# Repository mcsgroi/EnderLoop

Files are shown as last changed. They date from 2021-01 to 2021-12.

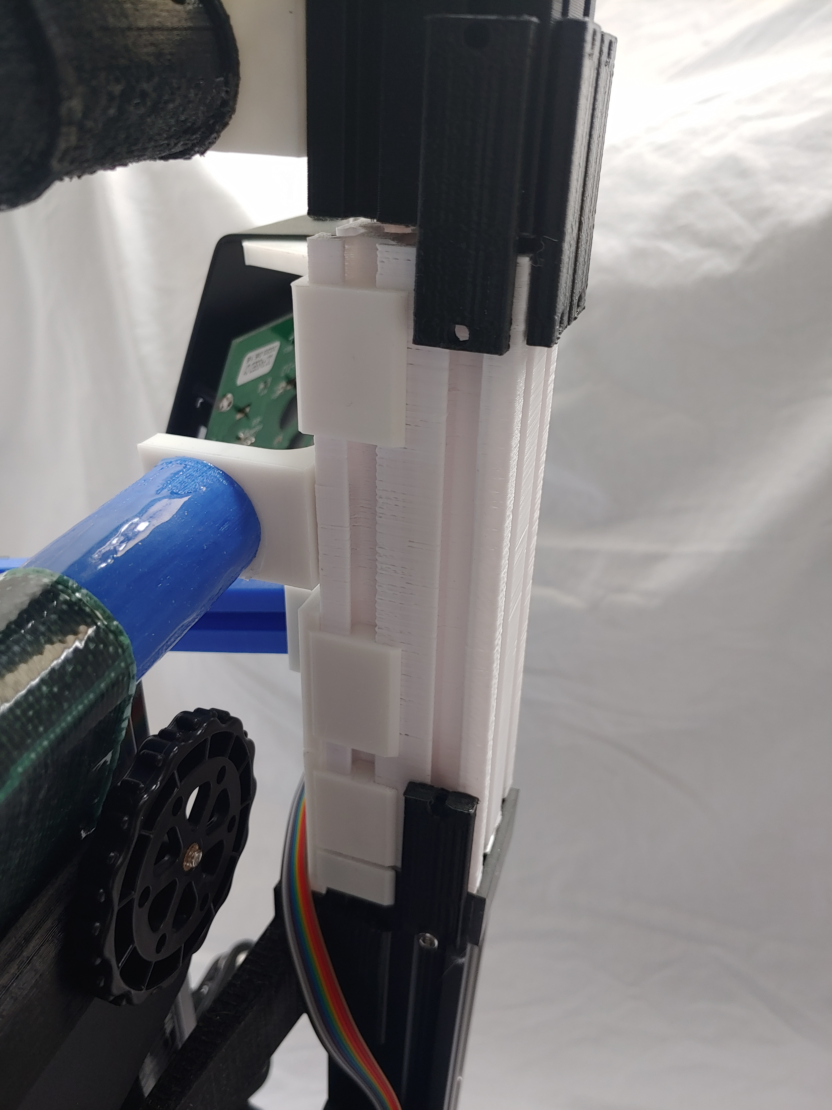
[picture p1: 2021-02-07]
Images/Printer/bottom3.jpg

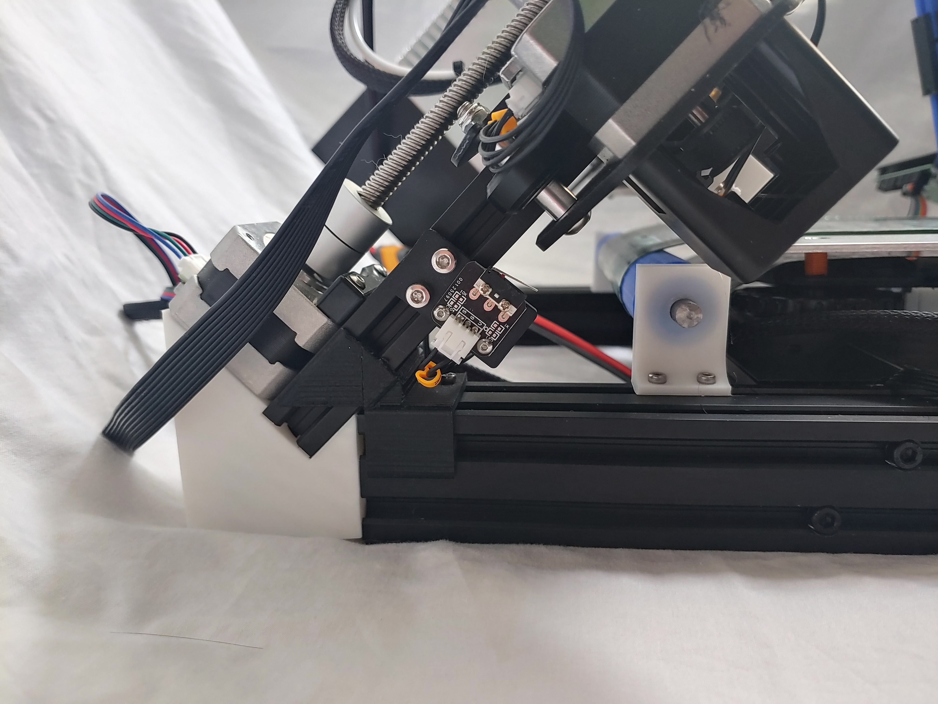
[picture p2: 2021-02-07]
Images/Printer/left5.jpg

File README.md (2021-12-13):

# EnderLoop
This supports around a 110x200xinfinity bed size.

[Here](https://www.youtube.com/watch?v=L337KpcwrPk&feature=youtu.be)'s a great video with Adam at PowerBelt3D discussing the EnderLoop.

### Donations
If you find this project helpful and want to send me a cup of coffee, feel free to use this button



&nbsp; 
&nbsp;  
&nbsp;  
**What's in this project:**

#### Pictures
I've attached a few pictures. Models in the printer pictures should mirror what is in the latest source files. Any differences should be minimal and are usually just that I'm running a slightly older version of the model to save on plastic waste. I've also included some test print pics to demonstrate the quality of what I'm getting off of the EnderLoop. In the pictures with two benchies, the black one is off of the belt printer whereas the white one is from a CR-6 SE as a comparison point.

#### Models
Not all of these models are required. I have included a list of what you'll need to print out and how many of each.

#### Firmware
The firmware will need to be flashed to the printer before you attempt to use it. I've included information on this in the instructions, but I've included my latest build of the firmware as well as the source in case you feel like modifying it. If you notice any issues feel free to open an issue or a PR on Github.

#### BlackBelt Cura Config
This is the configuration for the slicer. I've also included a couple snapshots in the pictures folder of what I'm using for settings on my printer currently, but keep in mind that any number of variables could change those for you (material, printer "quirks", etc.).

#### Test Models
Some test models for verifying the printer (esteps, angle, and long print adhesion). Note that the long print, as you'd probably expect, uses a large amount of material so, if you want to print that, I'd dial in smaller prints first.

### Versions
Check under the releases tab for stable snapshotted versions of this project. You can always use what is in the master branch, but since it is fluctuating with new work, there may be incorrect information or incompatible parts/software (though I try to keep everything in sync).

## Note
This is still a work in progress and you will most definitely find issues. Currently, I've identified a couple outstanding problems in my build:
1. Adhesion. I'm just gonna say outright that this isn't terrible adhesion. It's just not as good as I like it. It really depends on the model height and surface area touching the belt. You can improve the adhesion slightly by "scuffing" the surface of the belt with sandpaper.
2. Slight angle on some parts. I believe this has to do with esteps or cooling.

Most of the remaining issues are fairly minor and should either be small model updates or software tweaks.

If you experience any issues, they are most likely a result of bed leveling. I learned this the hard way so certainly check this first. Bed leveling a belt printer is trickier than with a "normal" printer and can cause some strange issues (adhesion, angled prints, head collisions, etc.)

Lastly, I'll note, and this is less of an issue and more of a limitation, but this will print slower than a normal printer due to the lead screw being used as the "de facto Y axis".

### Parts

#### Printed Parts
* 2 - AngledSupport
* 2 - BedStandV2
* 2 - BeltSlide
* 1 - EndSensorHolder
* 2 - GantryBraceBottom
* 1 - GantryBraceHolderLeft
* 1 - GantryBraceHolderRight
* 2 - GantryBraceTop
* 1 - LcdHolder
* 1 - LeftBeltClip
* 1 - ModifiedMotorHolder
* 1 - PartCoolerVent
* 1 - RightBeltClip
* 2 - Updated45ZHolder
* 2 - UpdatedAxle or UpdatedAxleCrowned or UpdatedAxleSteelRod
* 4 - UpdatedYIdler
* 2 - YExtension
* 2 - YExtensionClamp
* 11 - YExtensionSupport

##### Optional

1 - Scraper

###### Extension rollers
* 2 or 3 - UpdatedAxle
* 4 or 6 - UpdatedYIdler
* 2 - Yextension
* 8 - YExtensionSupport

#### Purchased Parts
##### Belt
Currently there are 3 options (there may be a 4th option when Creality's CR-30 belt is officially released):
1. Buy a custom belt. There are some sites that are willing to sell a custom belt. I believe BuildTak is willing to custom make a belt, however the price is fairly steep (based on my research on the WhiteKnight printer).
2. DIY. I'll include a section here on how to make a belt yourself should you want to. Note that it's going to take some patience to get a clean surface and the performance (adhesion and ability of the roller to grip the belt) will be worse than option 3. The price point for this option is also going to be about the same as option 3.
3. [POWERBELT3D Belt](https://powerbelt3d.com/product/formula32-conveyor-belt-for-enderloop/). I've reached out to Adam at PowerBelt and he was willing to list a custom belt that he has been working on that is specifically designed for the EnderLoop on his store. This is what I use right now and has pretty good characteristics. A couple of notes from the PowerBelt folks on this:
	* For PLA, we recommend a bed temperature of 60-70C.  
    * For PETG and TPU, they recommend a bed temperature of 70-80C. PETG tends to stick  _very_  well to the Polyester top layer, and might rip the material. They also recommend applying glue stick to the conveyor belt as a release agent to prevent this. If tearing still occurs, increasing the speed of outer contour that contacts the conveyor belt may help.

#####  Timing Belt
You have a few options. My recommendation would be to purchase https://www.amazon.com/gp/product/B081GYFQM3/ref=ppx_yo_dt_b_asin_title_o07_s00?ie=UTF8&psc=1
These are a little over 8mm wide. You'll note that this is wider than standard 2GT time belts (typically 6mm).
This helps it get better traction.
If you are looking to save a few bucks, you should also be able to use the extra timing belt in the Ender 3 
kit you don't need (for the original y axis). I would recommend looking up videos on joining timing belts, 
but you should be able to cut each end in the middle of a tooth (keeping note of how long you want the loop), 
rough up the back of the belt (smooth side) with sand paper, and glueing them together with a piece of 
cloth or ribbon on the roughed up side for extra adhesion support. If you find that this isn't enough to hold the belt together, 
you can try to use braided fishing line (https://www.amazon.com/gp/product/B076CMSC63/ref=ppx_yo_dt_b_asin_title_o09_s00?ie=UTF8&psc=1) 
to stitch the adhered ends together.

#####  Belt Motor
The Y motor on the Ender 3 simply doesn't have enough torque to be able to turn the belt.
I ended up purchasing https://www.amazon.com/gp/product/B07PS4BMSN/ref=ppx_yo_dt_b_asin_title_o03_s00?ie=UTF8&psc=1.
It is a Nema 17 stepper motor that draws less than 2 Amps (this is the max that the drivers on the Ender 3, regardless of version, will support).
That stepper motor I linked also coincidentally has an extra cable with it. You will either need this, 
another long stepper cable, or to make your own cable 
(https://www.amazon.com/gp/product/B077LYP4T9/ref=ppx_yo_dt_b_asin_title_o02_s00?ie=UTF8&psc=1). This is to accomodate the longer distance to the 
original Z motor which mounts at the back of the printer now, instead of the middle.
##### Pulley
Since you need to install a new motor, you will also need a new pulley for the belt motor. I used https://www.amazon.com/gp/product/B07BT6N12L/ref=ppx_yo_dt_b_asin_title_o05_s00?ie=UTF8&psc=1
#####  Springs
You will need better springs for the bed than the Ender 3 comes with. I ended up buying this assortment https://www.amazon.com/gp/product/B07V6YCYP5/ref=ppx_yo_dt_b_asin_title_o00_s00?ie=UTF8&psc=1
##### "Grippy" Paint
You will also need flex seal or another suitably "grippy" paint on coating to put on the axle.
##### Lubricant
You will need a lubricant for all of the roller ends. I always use Super Lube.

##### Steel Rods - Optional
I'm listing this here even though it is optional because I **highly** recommend this. These are for the rollers to ensure they don't flex inward. You can make this work without them, but the purely 3d printed one's can't continually handle the stress of sitting without spinning with the belt tensioned on them. With that in mind, you'll want "Tight-Tolerance Oil-Hardening O1 Tool Steel Rod, 0.3020" Diameter, 3 Feet Long" from https://www.mcmaster.com/steel-rods/tight-tolerance-multipurpose-oil-hardening-o1-tool-steel-rods/.

##### Fasteners
* T Nuts - I would recommend buying an assortment pack like https://www.amazon.com/gp/product/B07FPLZXTF/ref=ppx_yo_dt_b_asin_title_o02_s00?ie=UTF8&psc=1
although you mainly need M3 sized parts (and the Ender 3 kit comes with a couple extra M4 T nuts in case you go that route).
* M3 washers to use as spacers for the hotend. You shouldn't need more than 4.
* Assorted M3/M4 screws, mostly M3 8mm. I would recommend buying an assortment to slot in. 
Most of it is fairly flexible in what you use. Most holes in the parts I designed are for M3 screws, but you 
can enlarge the holes in the models if you go with another screw size.
* 2 M3 20mm screws and 2 M3 nuts for attaching the hot end lower on the print head mount plate.
* 4 M5 screws for attaching the gantry to the base. I would recommend they be 40-50 mm long since they will be holding the gantry, but the length is fairly flexible.
* 2 M5 screws and 2 M5 nuts for attaching the lcd screen to the mount. I would recommend around 30 mm long, but, again, that's fairly flexible. 

#### Tools
I've tried to make this install as "tool-less" as possible to make it accessible. That said, I've determined that in order to make this as functional as possible, there are a couple tools you'll need (or you can go to your local metal/machine shop to have done for you). 
* Drill with titanium bits (or another bit that can drill steel)
* Dremel with a diamond coated cutting bit (or another bit that can cut steel)

#### Optional:
* You may want to consider purchasing a few nylon washers to go above the springs, but below the heated bed. This will prevent damage to the heated bed from the metal spring. This is more of an Ender 3 design upgrade than an EnderLoop mod component, but I think it's worth mentioning, especially if you replace the default springs with stronger ones.
* I sadly managed to break endstops while I was tinkering with design and assembly. If you find yourself in a similar predicament,
these work as replacements https://www.amazon.com/gp/product/B08G7Y5C63/ref=ppx_yo_dt_b_asin_title_o01_s00?ie=UTF8&psc=1
* I also unfortunately managed to fry my mainboard (specifically a driver) while I was tinkering and ended up replacing it with https://www.amazon.com/gp/product/B07TYFJ924/ref=ppx_yo_dt_b_asin_title_o01_s00?ie=UTF8&psc=1. These boards are fantastic because the drivers on them are INCREDIBLY quiet. The loudest part on the printer after installing one of these becomes the fans.
* If your mainboard is V1.1.5, you will need either an Arduino or a USBTiny (https://www.amazon.com/gp/product/B07S9BX98K/ref=ppx_yo_dt_b_asin_title_o04_s00?ie=UTF8&psc=1)

#### DIY Belt Instructions
 In order to keep this lower cost, the backing is steel shim, which I taped into a belt using kapton tape.
I then coated the hole belt in kapton tape. Your other options are PET tape or PEI sheets with an adhesive coating between the sheet and the steel shim. 
Steel shim link: https://www.mcmaster.com/steel-shim-stock/shim-stock-6/
Instructions on sizing this are further down in the assembly information.

### Firmware
You will note that there are a few combinations of mainboards/drivers that ender 3's can come with:
##### Motherboards:
* V1.1.5
* V4.2.2
* V4.2.7

##### Drivers:
* HR4988
* A4988
* TMC2208
* TMC2225

The precompiled firmware is meant for V4.2.7 and TMC2225 drivers (should also work with TMC2208 drivers). If you are using any other board/driver combination, 
you will need to edit the firmware I provided. 
Best I can tell, it seems that V1.1.5 comes with A4988, V4.2.7 comes with TMC2208 or TMC2225, and V4.2.2 can come with any 
of the drivers listed.
V4.2.7 and V4.2.2 are simple enough to program. Simply place a compiled binary on a microsd card and insert into the printer. 
When you turn it on it will flash the printer. If it complains about mismatched EEPROM, just ignore it and update the 
EEPROM in the menu on the printer (lots of examples on the internet). If you have a V1.1.5, you will need to flash the firmware using
and Arduino or a USBTiny (https://www.amazon.com/gp/product/B07S9BX98K/ref=ppx_yo_dt_b_asin_title_o04_s00?ie=UTF8&psc=1).
Not gonna go into to many details here as there's plenty of information on flashing the firmware available online.

### Slicer
You will need to install BlackBelt Cura to do belt printing. Once installed, find the install directory (C:\Program Files\BlackBelt Cura 3.6.0\resources on Windows)
and copy/paste the Config folders I included here. This will prompt to overwrite a file, say yes. The config I included overwrites the BlackBelt default one. 
This should be fine since most people who can afford a BlackBelt probably aren't making this ;)

### Wiring
As far as wiring goes, there are a few things to keep in mind. Look at the stepper motor cable wire order in the connectors (the prebuilt connectors that come with the printer).
You'll note the middle two wires are inverted. Make sure you keep a close eye on whether a cable is supposed to have those wires
inverted or not. The motor I purchased to drive the belt did not want those wires inverted, but all the Ender 3 motors do.
One other thing to keep in mind is that all belt printers treat what we would normally consider the Y direction as Z. To 
accommodate this, you will need to plug the belt motor into the Z slot on the mainboard and the gantry motor into the Y slot on the mainboard.
You will also need to plug the gantry end stop switch into the Y slot on the mainboard. You don't need a Z end stop switch (since there is no zero on a belt). 
Everything else should be wired the same.

### Print settings
Everything was printed somewhere between a 20-30% infill except for the axles which were printed at 60% infill and the RightBeltClip which was printed at 80% infill.

You also may find the part tolerances to be too tight or too loose depending on how your printer is calibrated. You can either modify the models slightly to increase/decrease the size or use the horizontal expansion setting in Cura adjust the part prints.

### Assembly
Assembly is fairly straight forward and most of it should make sense off of the pictures. 
To start, you will need to strip down a few parts that are on the Ender 3 already. 
Most of the parts you will be taking off are on the bed. You won't need the timing belt, motor, or aluminum extrusion directly under the bed. I've attached a picture to give you an idea of most of the parts you won't need.

You will need to keep the metal plate, screws, and tightening wheels right under the bed. This metal plate is what you will attach to the BedStand model and you should be able to attach it in the same way the wheels were originally attached (same nuts and bolts).
Depending on how tight this model is to your aluminum extrusion, you can use T nuts and screws to secure the BedStand more tightly. As far as replacing the springs that come with the Ender 3, I would recommend experimenting with a few different spring tensions. I used two different varieties of spring since one side of my printer needed to be tightened down more than the other. I would also recommend putting a nylon washer on top of each spring (just under the heated bed) to prevent the spring from scraping the heated bed.

The gantry is mounted at a 45 degree angle. This is accomplished with the Updated45ZHolder and the AngledSupport files. Slide the AngledSupport on first to the aluminum extrusion base and then slide the gantry extrusion into it. Lastly, slide the ModifiedMotorHolder onto the end of the gantry extrusion and screw the Updated45ZHolder into the gantry extrusion (these screws should be the ones that come with the printer) 
and the base extrusion (these will be the longer M5 screws mentioned on the parts list). I only used two screws on the base extrusion since that seemed sufficiently sturdy.

The hot end needs to be lowered on the print head. This is where the drill with a titanium bit comes in. You will be drilling a hole to accommodate the M3 20mm screws that attaches the hot end to the print head plate. I've attached a picture of this, but basically the holes should be drilled as low as possible without reaching the point on the steel where it starts to curve. It should also be vertically aligned with the original screw holes. Once you've done this, you can mount the hot end using the M3 20mm screws and M3 nuts using 4 M3 washers (2 per screw) as spacers between the hot end and the steel print head plate. Note, these screws need to extend past the back of the steel print head plate exactly the right amount so you can install the washer. If it goes to far, the screws will grind on the aluminum extrusion when it slides left to right and you will run into problems.

Most likely the silicon sock that comes with the Ender 3 will have material that covers the brass nozzle on the hot end. You'll want to trim the silicon that covers the brass nozzle or it will hit the bed or your in progress print due to the 45 degree print angle. 
You'll also need to remove the print fan vent piece from the side of the print head and replace it with the PartCoolerVent.

The print head is mounted 90 degrees from how a standard Ender 3 is constructed. To handle this, you need to unscrew the wheels on the print head and mount the LeftBeltClip and RightBeltClip under those screws.
The X axis timing belt slides into the slots on those two parts. Note that you'll want to install the timing belt on the LeftBeltClip before you resecure the wheels.
Once that is in place, you should be able to install the print head on the aluminum extrusion and install the timing belt around the motor (like you normally would).
Lastly, you'll need to install the EndSensorHolder on the side of the aluminum extrusion that the hot end is on. Slide it as far left as you can without the print head hitting the metal support that attaches to the extrusion. This is installed using a T nut. You will need to remove the limit switch on the X axis (it's at the end of this rod under a plastic cover where the timing belt runs). This limit switch can then be screwed onto the EndSensorHolder.

Next you will add the gantry support pieces. This will involve attaching the GantryBraceHolderLeft on the left aluminum extrusion on the base and the GantryBraceHolderRight on the right aluminum extrusion on the base. This provides a socket hole on top to install the GantryBraceBottom into each of them. On top of the GantryBraceBottom you will use 8 (4 on each) to attach the GantryBraceTop's. These will then screw in to the top of the gantry using the outermost screw hole (you'll need to remove the screw that was there already) and a couple extra M5 screws you should have lying around from stripping parts off of the Ender 3.

The next step is to extend the base. You will need to install two YExtension pieces at the front of the base (towards you) using two YExtensionClamp's and 4 YExtensionSupport's. I would recommend sliding the ModifiedMotorHolder onto the left YExtension before clamping the YExtension in place.
These will be held in place using T nuts. 
You can then mount the ModifiedMotorHolder using T nuts on the left YExtension. 

Note, for all of the roller instructions that follow, you will need to apply a lubricant to the rollers where they contact the idlers.
You have 3 options for the rollers. 
1. UpdatedAxle - This is just a standard 3d printed roller.
2. UpdatedAxleCrowned - This is a 3d printed roller with crowning in the middle to keep the belt inline.
3. UpdatedAxleSteelRod - This is a 3d printed roller that you insert a steel rod into the middle of for support.

I would recommend option 3. Should you go this route, the only additional work you need to do is:
1. Cut the 3 ft steel rod into two, roughly 11in pieces (slightly longer is fine, but I wouldn't go shorter than that).
2. Insert the steel rod pieces into two UpdatedAxleSteelRod prints. If it won't go through, I'd run a drill bit of a _slightly_ larger diameter through the inside of the model to loosen the tolerance.
3. If the steel rod sticks a bit, that's fine. I used a hammer to finish the job. Having it tight is perfectly fine (and actually makes it a bit simpler to install). If it isn't tight, you'll want to apply an adhesive to keep it in place so it doesn't slide out.

No matter which of the roller options you choose, you will install one of the rollers using two UpdatedYIdler's and T nuts at the back of the printer (just behind the bed).
The next roller you'll be installing will be the one that the motor drives. The roller model itself won't be able to grip the belt as it stands. You need to coat this roller, including the teeth, in a thin coating of something "grippy". I found FlexSeal paint worked well.
Then you will need to mount this roller using two UpdatedYIdler's and T nuts at the front of the printer (between the ModifiedMotorHolder and the bed).

You then install two BeltSlide's. One goes on the back side of the print bed (on that metal plate under the bed, kind of between the tightening wheels) and one on the front side (between the other two tightening wheels).

---
###### DIY Belt Sizing
You will cut the steel shim based on the width between the two guard bumps on the rollers and the length a little longer than necessary to go around the rollers, over the bed and over the belt slides.
Note that the steel shim is super sharp when cut, but you should be able to file it down.

---

The belt (regardless of which option you chose) can then be fed under the axle, over the two BeltSlide's (inside the small teeth that hold it), under the other axle, and back over the bed.

---
###### DIY Belt Coating
You will want to tape it tight and straight (if either side is longer than the other, prints won't work well). Then run Kapton tape lengthwise over the belt to cover it for better print adhesion.
Less deformities in the tape is better as it will increase adhesion and lower model warp.

---

--- 
###### PowerBelt Belt Installation
From the folks at PowerBelt: https://youtu.be/ShYZX8OavIs 

I will also note here that it can be helpful to lightly scuff the surface of the belt with sandpaper to increase the adhesion a bit.

--- 

You will want to install the belt motor into the ModifiedMotorHolder and attach a pulley to the motor axle.
The timing belt will then go around the teeth on the axle and the pulley.
Then you can install the LcdHolder on the right YExtension using T nuts and some screws (don't recall the size on these, had a few laying around).

#### Optional
Lastly, if you want an extension with rollers for longer prints, you can print out additional YExtension's, YExtensionSupport's (4 for each extension, go on the bottom half), and UpdatedYIdler's/UpdatedAxle's (as many as you'd like really, 2 UpdatedYIdler's per UpdatedAxle).

### Sources
I went through quite a few sources online to learn enough to make this happen. I wanted to list a few to acknowledge and also for anyone who wants to learn more. In particular I wanted to mention the Infinity Ender project on Thingiverse which provided a lot of the part inspiration. I also wanted to mention the aluminum extrusion Thingiverse entry in this list. I based my y extensions off of that model.

https://www.thingiverse.com/thing:4267968

https://www.instructables.com/Turn-Your-3D-Printer-Into-a-Factory-Automatically-/

https://hackaday.io/project/114738-automatic-infinite-3d-printer/log/146614-ejecting-parts-from-workhorse-3d-printer-mk-3/discussion-122983

https://www.thingiverse.com/thing:280318

https://hackaday.io/project/114738/instructions

https://www.reddit.com/r/3Dprinting/comments/4tc1x8/part_removal_conveyor_belt_thingy_for_larger/

https://www.thingiverse.com/thing:3434404

https://forum.duet3d.com/topic/8332/modded-ender-3-conveyor-concept/2

https://blackbelt-3d.com/the-blackbelt-3d-printer/

https://www.youtube.com/watch?v=czozhy7kjwc&feature=youtu.be

### License
EnderLoop is licensed under the [Creative Commons - Attribution - Non-Commercial license](https://creativecommons.org/licenses/by-nc/4.0/).

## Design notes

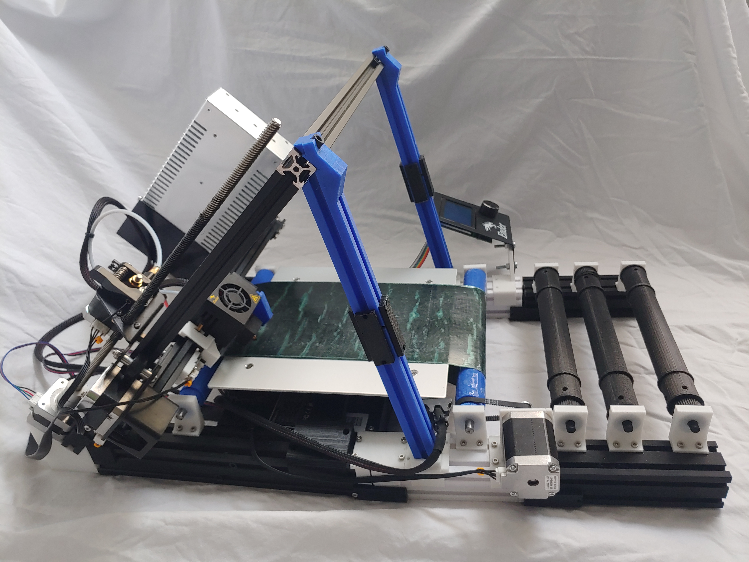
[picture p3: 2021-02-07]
Images/Printer/overview3.jpg

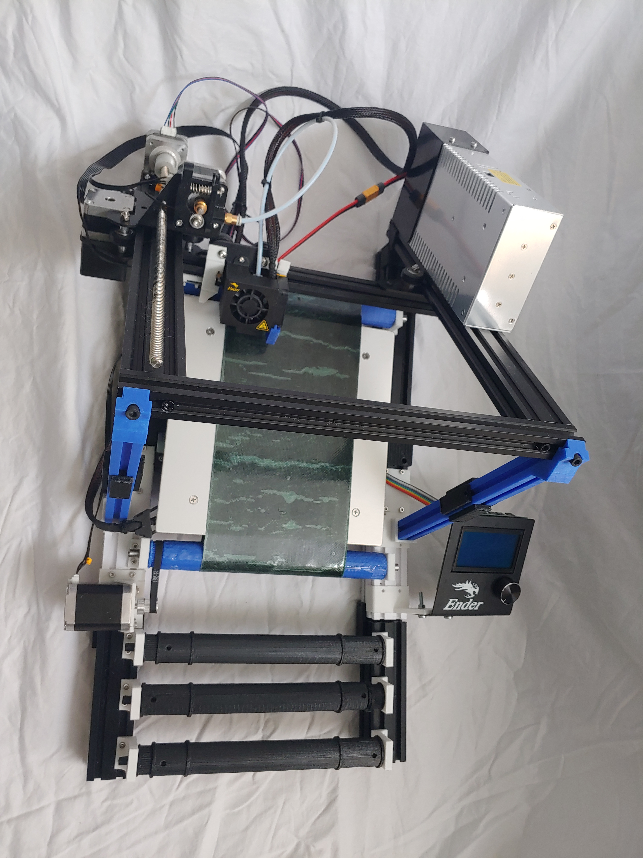
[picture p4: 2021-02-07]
Images/Printer/overview1.jpg

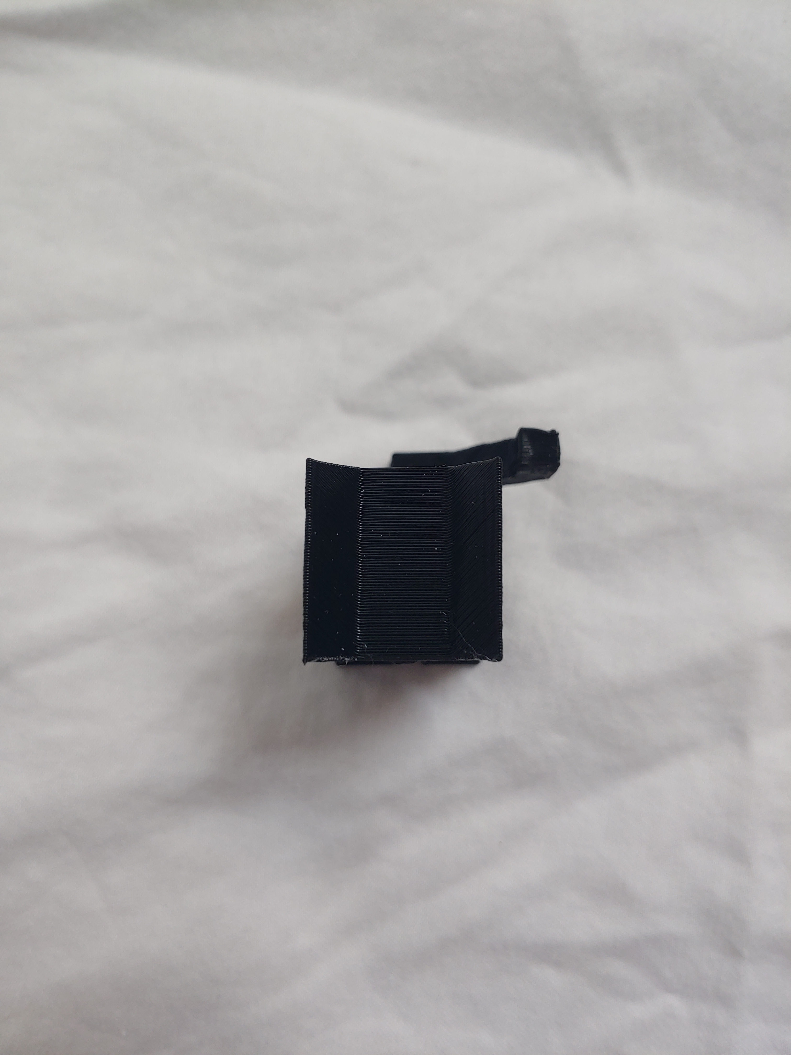
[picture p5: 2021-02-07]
Images/Models/calicat1.jpg

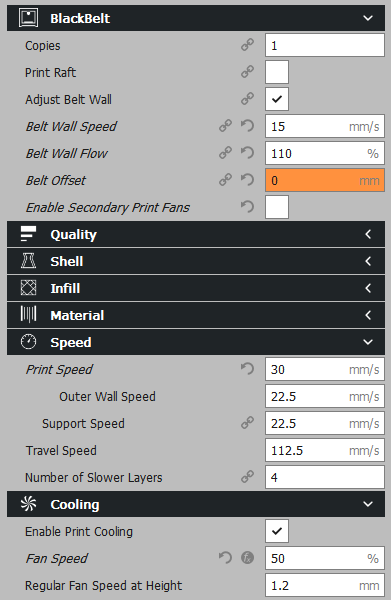
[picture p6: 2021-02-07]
Images/Cura Settings/CustomSettings.png

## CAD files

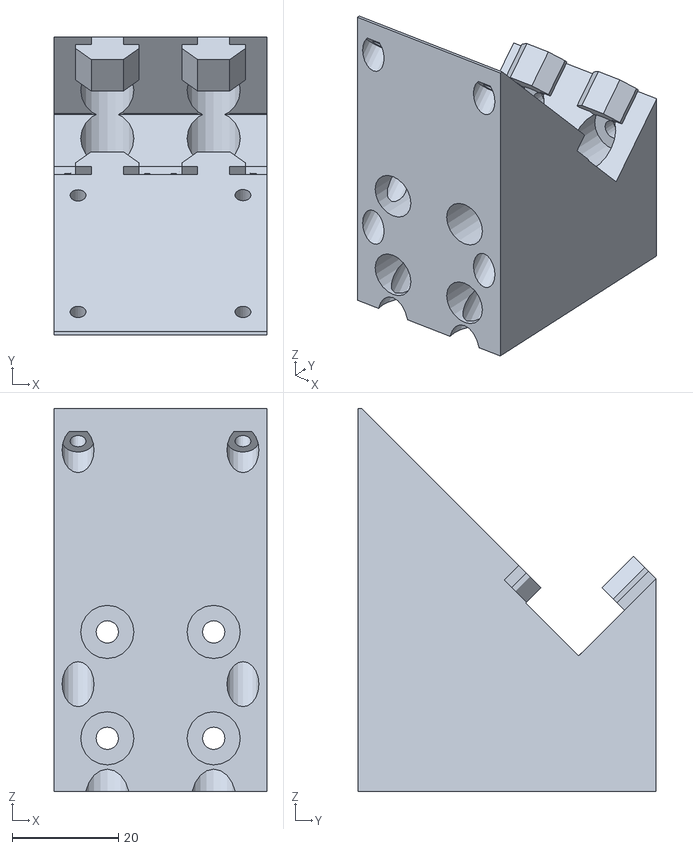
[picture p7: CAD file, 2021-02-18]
Models/Updated45ZHolder.stl
40.0 x 56.0 x 72.0

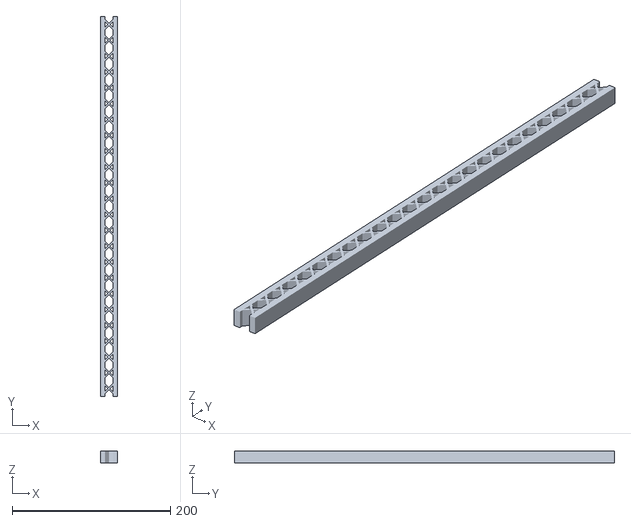
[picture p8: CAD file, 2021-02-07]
TestModels/BeltTest.stl
22.0 x 480.0 x 15.0

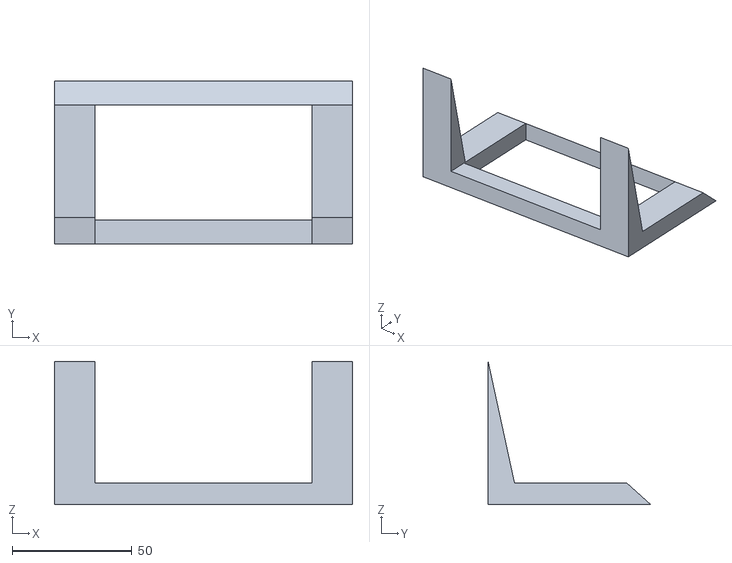
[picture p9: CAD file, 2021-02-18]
Models/Scraper.stl
124.5 x 68.0 x 59.9

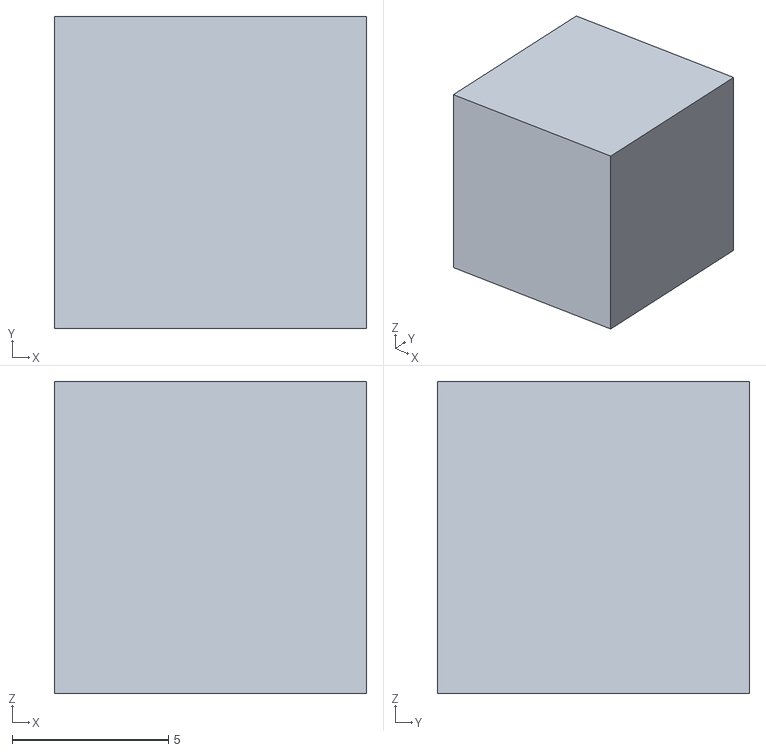
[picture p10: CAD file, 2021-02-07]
TestModels/SmallBox.stl
10.0 x 10.0 x 10.0

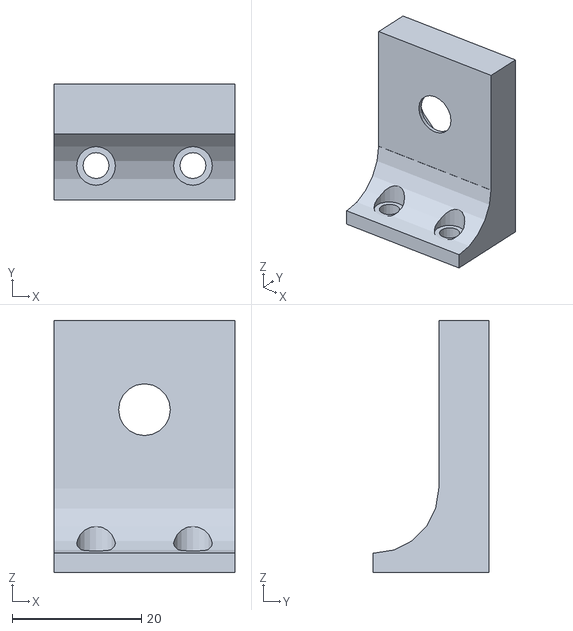
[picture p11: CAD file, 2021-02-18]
Models/UpdatedYIdler.stl
28.0 x 18.0 x 39.0

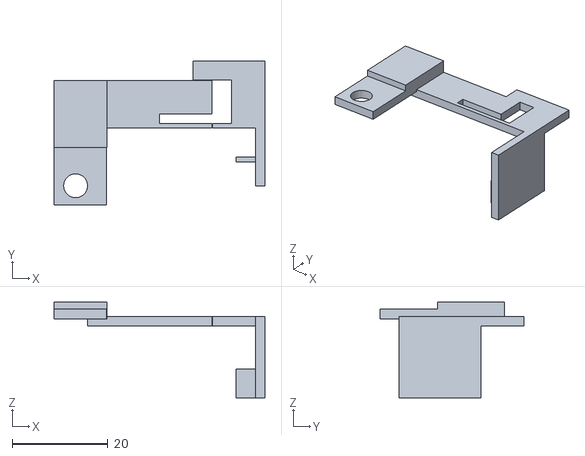
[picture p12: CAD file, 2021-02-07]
Models/RightBeltClip.stl
44.0 x 30.0 x 20.0

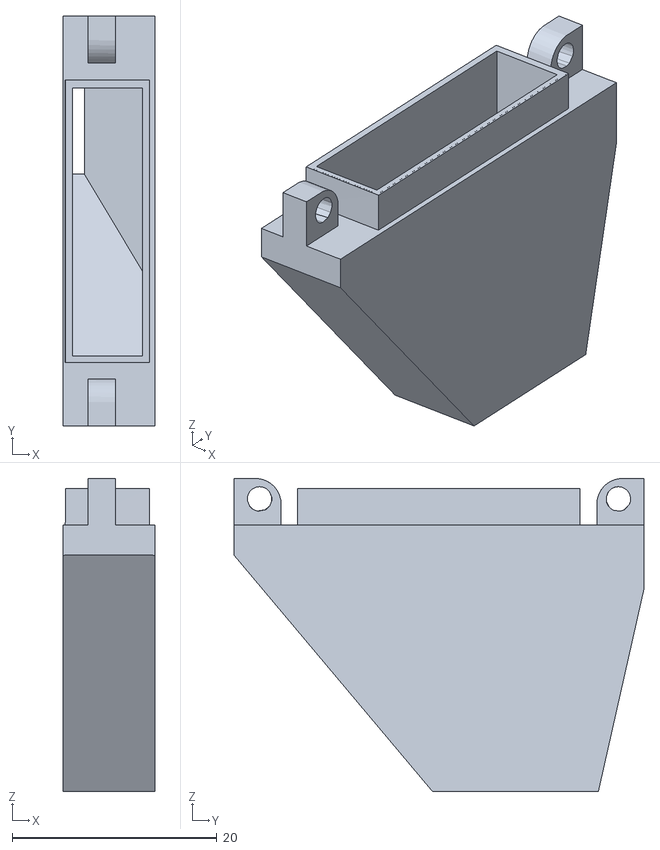
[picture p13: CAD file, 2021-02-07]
Models/PartCoolerVent.stl
8.95 x 40.0 x 30.6

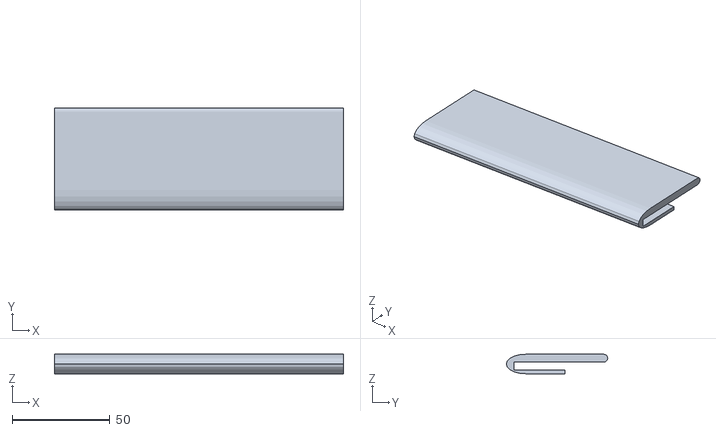
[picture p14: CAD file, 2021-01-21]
Models/BeltSlide.stl
148.0 x 52.0 x 10.0

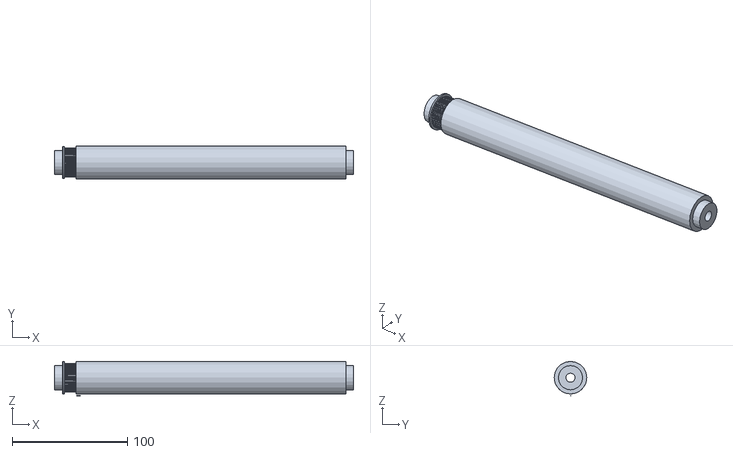
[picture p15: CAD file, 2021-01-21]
Models/UpdatedAxleSteelRod.stl
259.0 x 28.3 x 29.6

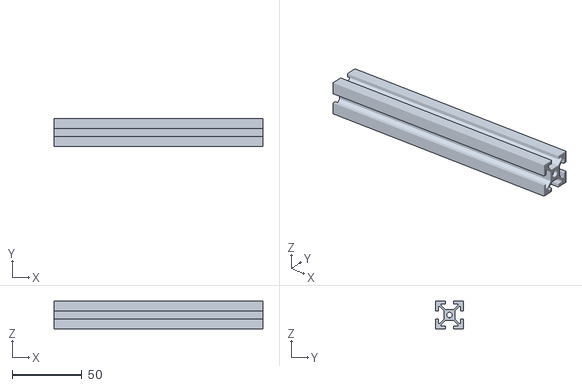
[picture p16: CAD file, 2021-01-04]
Models/GantryBraceBottom.stl
150.0 x 20.0 x 20.0

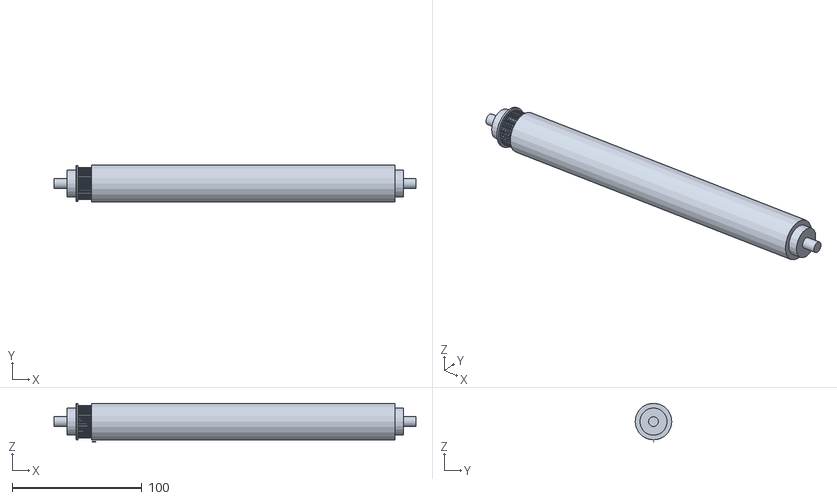
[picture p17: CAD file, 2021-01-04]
Models/UpdatedAxle.stl
278.7 x 28.3 x 29.6

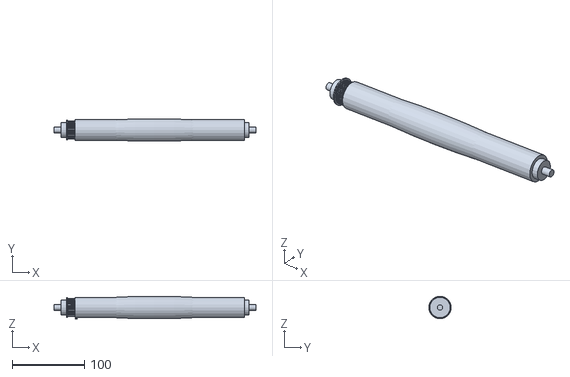
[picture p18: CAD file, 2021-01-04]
Models/UpdatedAxleCrowned.stl
278.7 x 31.0 x 31.0

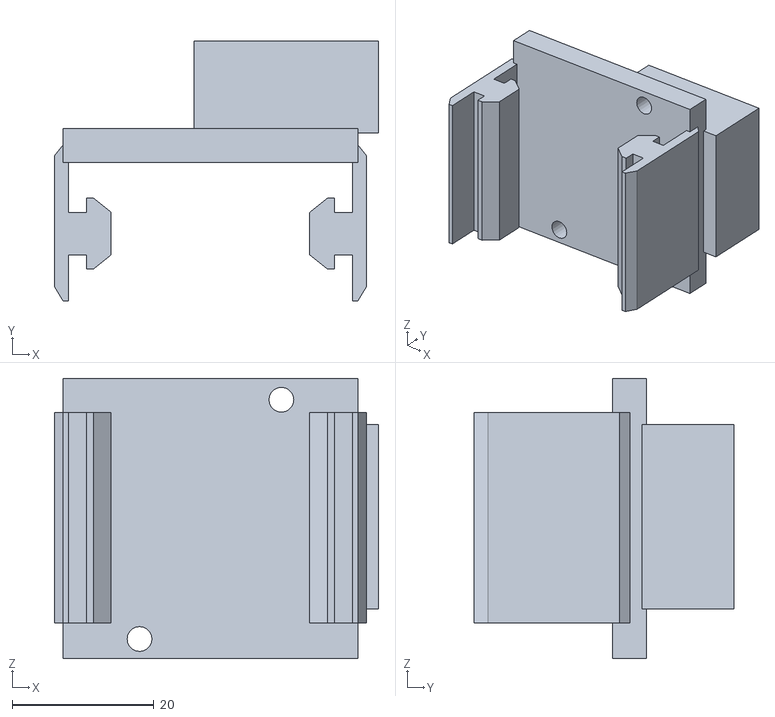
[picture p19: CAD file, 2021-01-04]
Models/GantryBraceHolderRight.stl
45.7 x 36.7 x 39.5

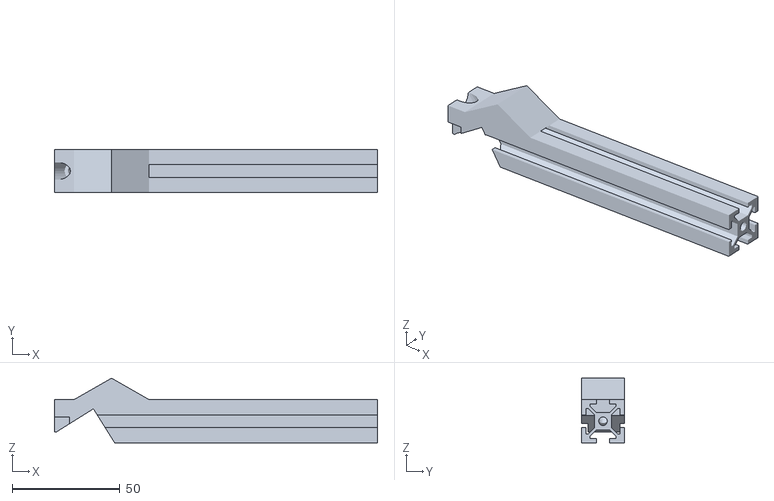
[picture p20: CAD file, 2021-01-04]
Models/GantryBraceTop.stl
150.0 x 20.0 x 30.0

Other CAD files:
Models/GantryBraceHolderLeft.stl
Models/BedStandV2.stl
Models/EndSensorHolder.stl
Models/AngledSupport.stl
Models/LcdHolder.stl
Models/LeftBeltClip.stl
Models/ModifiedMotorHolder.stl
Models/YExtension.stl
Models/YExtensionClamp.stl
Models/YExtensionSupport.stl

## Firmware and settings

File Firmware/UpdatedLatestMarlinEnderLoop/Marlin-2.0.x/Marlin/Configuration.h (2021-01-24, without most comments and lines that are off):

#pragma once
#define CONFIGURATION_H_VERSION 020007
#define ENDER3_V422_BOARD
#define V422_TMC2208_BOARD
#define EZABL_POINTS 3
#define EZABL_PROBE_EDGE 35
#define EZABL_FASTPROBE
#define CUSTOM_ESTEPS_VALUE 463
#define HIGH_TEMP_THERMISTOR_TEMP 290
#define X_HOME_LOCATION -10
#define Y_HOME_LOCATION -10
#define LINEAR_ADVANCE_K 0
#define SERIAL_PORT 1
#define BAUDRATE 115200
#define CR10_STOCKDISPLAY
#define RET6_12864_LCD
  #define MOTHERBOARD BOARD_CREALITY_V427
#define CREALITY_Z_STEPS 419.9
#define DEFAULT_AXIS_STEPS_PER_UNIT   { 80, CREALITY_Z_STEPS, 72.7, 95 }
#define DEFAULT_MAX_FEEDRATE          { 500, 30, 30, 25 }
#define DEFAULT_MAX_ACCELERATION      { 500, 300, 25, 1000 }
#define DEFAULT_ACCELERATION          500
#define DEFAULT_RETRACT_ACCELERATION  500
#define DEFAULT_TRAVEL_ACCELERATION   1000
#define CLASSIC_JERK
  #define DEFAULT_XJERK 10.0
  #define DEFAULT_YJERK 0.3
  #define DEFAULT_ZJERK  10.0
#define DEFAULT_EJERK    5.0
#define SHOW_BOOTSCREEN
#define EXTRUDERS 1
#define X_BED_SIZE 110
#define Y_BED_SIZE 200
#define Z_MAX_POS 999999
#define X_MIN_POS 0
#define Y_MIN_POS 0
#define USE_XMIN_PLUG
#define USE_YMIN_PLUG
#define USE_ZMIN_PLUG
#define X_HOME_DIR -1
#define Y_HOME_DIR -1
#define Z_HOME_DIR -1
#define TEMP_SENSOR_0 1
#define TEMP_SENSOR_1 0
#define TEMP_SENSOR_2 0
#define TEMP_SENSOR_3 0
#define TEMP_SENSOR_4 0
#define TEMP_SENSOR_5 0
#define TEMP_SENSOR_6 0
#define TEMP_SENSOR_7 0
#define TEMP_SENSOR_BED 1
#define TEMP_SENSOR_PROBE 0
#define TEMP_SENSOR_CHAMBER 0
#define DEFAULT_Kp 28.72
#define DEFAULT_Ki 2.62
#define DEFAULT_Kd 78.81
#define DEFAULT_bedKp 462.10
#define DEFAULT_bedKi 85.47
#define DEFAULT_bedKd 624.59
#define ENDSTOPPULLUPS
#define X_MIN_ENDSTOP_INVERTING false
#define Y_MIN_ENDSTOP_INVERTING false
#define Z_MIN_ENDSTOP_INVERTING false
#define X_MAX_ENDSTOP_INVERTING false
#define Y_MAX_ENDSTOP_INVERTING false
#define Z_MAX_ENDSTOP_INVERTING false
#define Z_MIN_PROBE_ENDSTOP_INVERTING false
#define Z_MIN_PROBE_USES_Z_MIN_ENDSTOP_PIN
#define ENDSTOP_INTERRUPTS_FEATURE
#define X_ENABLE_ON 0
#define Y_ENABLE_ON 0
#define Z_ENABLE_ON 0
#define E_ENABLE_ON 0
#define INVERT_X_DIR true
#define INVERT_Y_DIR true
#define INVERT_Z_DIR false
#define INVERT_E0_DIR false
#define INVERT_E1_DIR false
#define INVERT_E2_DIR false
#define INVERT_E3_DIR false
#define INVERT_E4_DIR false
#define INVERT_E5_DIR false
#define INVERT_E6_DIR false
#define INVERT_E7_DIR false
#define ENCODER_PULSES_PER_STEP 4
#define ENCODER_STEPS_PER_MENU_ITEM 1
#define Z_PROBE_OFFSET_RANGE_MIN -10
#define Z_PROBE_OFFSET_RANGE_MAX 10
  #define X_DRIVER_TYPE TMC2208_STANDALONE
  #define Y_DRIVER_TYPE TMC2208_STANDALONE
  #define Z_DRIVER_TYPE TMC2208_STANDALONE
  #define E0_DRIVER_TYPE TMC2208_STANDALONE
#include "Configuration_backend.h"

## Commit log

2020-11-22 Updated bed stand
    [BedStand.stl, BedStandV2.stl]
2020-12-28 Added pictures for assembly
2021-01-04 Update models, firmware, and cura config
    [Configuration.h, GantryBraceBottom.stl, GantryBraceHolderLeft.stl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]
2021-01-21 Update cura config, modify beltslide, add new axle with steel rod insert
    [BeltSlide.stl, UpdatedAxleSteelRod.stl]
2021-01-24 Update z acceleration max
    [Configuration.h]
2021-02-07 Clean up pictures, models and readme for new version
    [BeltTest.stl, PartCoolerVent.stl, RightBeltClip.stl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]
2021-02-07 Update README.md
    Added more info about replacing the springs on the Ender 3
2021-02-16 Update README.md
    Add end sensor holder information
2021-02-18 Update README.md
    Updated Y Idler ;model
2021-02-18 Replaced copied models with redesigned versions
    [Scraper.stl, Updated45ZHolder.stl, UpdatedYIdler.stl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]
2021-02-19 Update README.md
    Added PowerBelt belt product link
2021-02-25 Update README.md
    Reformat tip button
